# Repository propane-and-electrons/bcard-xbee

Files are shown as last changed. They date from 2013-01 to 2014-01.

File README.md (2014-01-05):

bcard-xbee
----------

Mid-2011, I had the idea of making a PCB business card. At the time I was working on Super Street Fire, and developing a [wireless solenoid controller](https://github.com/propane-and-electrons/wifire16) for triggering flame effects. I took the same basic idea, removed everything unnecessary (including the microcontroller), and set aside an area for contact info. With the remaining space, I found I could fit three optoisolator/MOSFET circuits comfortably.

The end result is this, a three channel wireless solenoid controller.

Yes, it is fully functional.

Please do not call me in the middle of the night and breathe heavily into the phone.

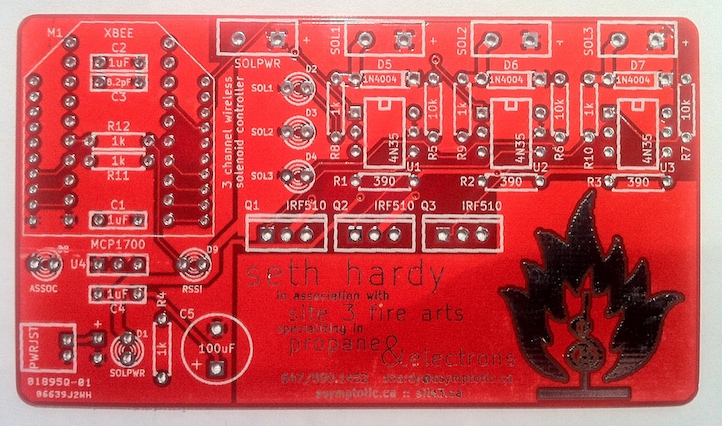
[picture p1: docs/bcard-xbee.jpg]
bcard-xbee photo


### Feature Summary

* No microcontroller!
* Uses XBee (Series 1 or 2, but 1 is easier) DIO lines to trigger outputs
* Three DC load channels switched via MOSFETs
* DC load power is optoisolated from control power
* Status LEDs on each output channel, and for XBee Association/RSSI indicators
* It has all my contact information on it so you know how to get in touch with me

### Design
I do give these cards out to people during normal business card exchange rituals. So, I chose to use only through hole parts: people often have little or no experience assembling electronics, so it was designed to be as easy as possible. XBee radios were also chosen for their ease of use.

The card itself is the same size as a normal business card. I have them made on 0.8mm FR4.

#### Power
The card has two separate power inputs: one for the control system, and one for the solenoid power that it switches. This allows the card to be powered off a 3.7V LiPo battery (with 2 pin JST header) or 3xAA/AAA battery pack, while switching 12V, 24V, or higher voltage DC to activate the solenoids.

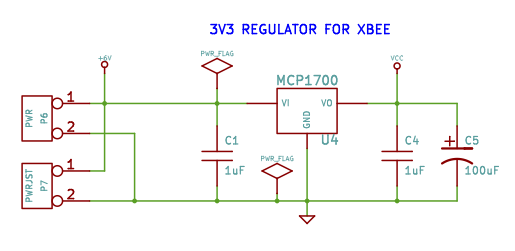
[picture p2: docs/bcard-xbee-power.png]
bcard-xbee photo


Since this was designed for fire art, having a separate solenoid power source allows a deadman switch inline, so the dangerous side can be shut down immediately while keeping the controller side active. The two sides are separated via optoisolators.

#### Data
The card uses an XBee radio (Series 1 or 2) for wireless communication. The card does not have a microcontroller on it: the outputs are triggered directly via DIO lines 0 – 2 of the XBee.

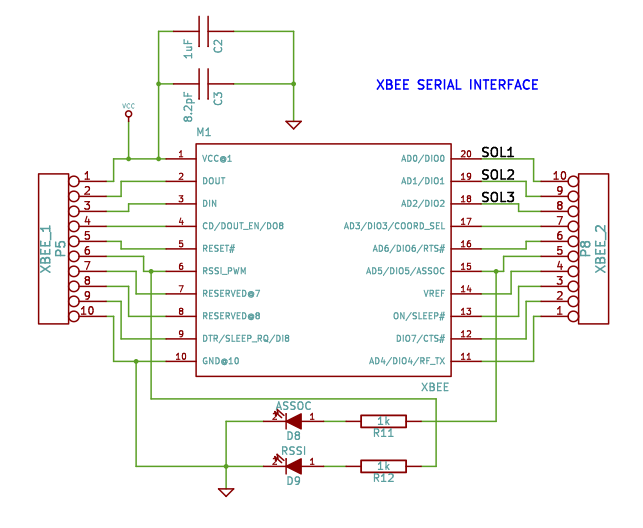
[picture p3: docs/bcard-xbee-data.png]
bcard-xbee photo


This means that a Series 1 radio is preferable, as they can do IO line pairing: change the IO line on the sending radio and it will trigger the output on the receiving radio automatically. Series 2 radios will also work using a remote AT packet to control the line.

#### Solenoid control
The solenoid power is switched using MOSFETs. Each channel has a LED indicator that lights up only when the channel is active.

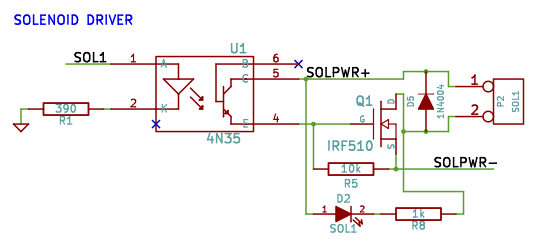
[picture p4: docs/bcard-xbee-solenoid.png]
bcard-xbee photo


### Documents

* [Schematic](docs/bcard-xbee-schematic.pdf)
* [Bill of Materials](docs/bcard-xbee-BOM.csv)

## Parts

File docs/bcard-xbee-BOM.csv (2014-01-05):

Designator | Package | Quantity | Part | Digi-Key Part
C1,C2,C4 | C2 | 3 | 1uF | 445-2858-ND
C3 | C2 | 1 | 8.2pF | 490-3764-ND
C5 | C2V8 | 1 | 100uF | P13459-ND
D1,D2,D3,D4 | LED-3MM | 1 | 3mm LED (red) | 754-1606-ND
D5,D6,D7 | D3 | 3 | 1N4004 | 641-1311-1-ND
D8,D9 | LED-3MM | 1 | 3mm LED (blue) | 754-1596-ND
M1 | XBEE | 1 | XBee Series 1 | XB24-AWI-001-ND
P1,P2,P3,P4 | 5MMSCREWTERM | 1 | 5mm screw terminal | ED2600-ND
P7 | JST2 | 1 | JST2 power header | 455-2257-ND
Q1,Q2,Q3 | TO220GDS_VERT | 3 | IRF510 | IRF510PBF-ND
R1,R2,R3 | R3 | 3 | 390 | 390QBK-ND
R4,R8,R9,R10,R11,R12 | R3 | 6 | 1k | 1.0KQBK-ND
R5,R6,R7 | R3 | 3 | 10k | 10KQBK-ND
U1,U2,U3 | DIP-6__300 | 3 | 4N35 | 516-1557-5-ND
U4 | SIL-3 | 1 | MCP1700 | MCP1700-3302E/TO-ND
XM1 |  | 2 | 2mm 10 pin header | S5751-10-ND
XU1,XU2,XU3 |  | 3 | 6DIP socket | A100203-ND

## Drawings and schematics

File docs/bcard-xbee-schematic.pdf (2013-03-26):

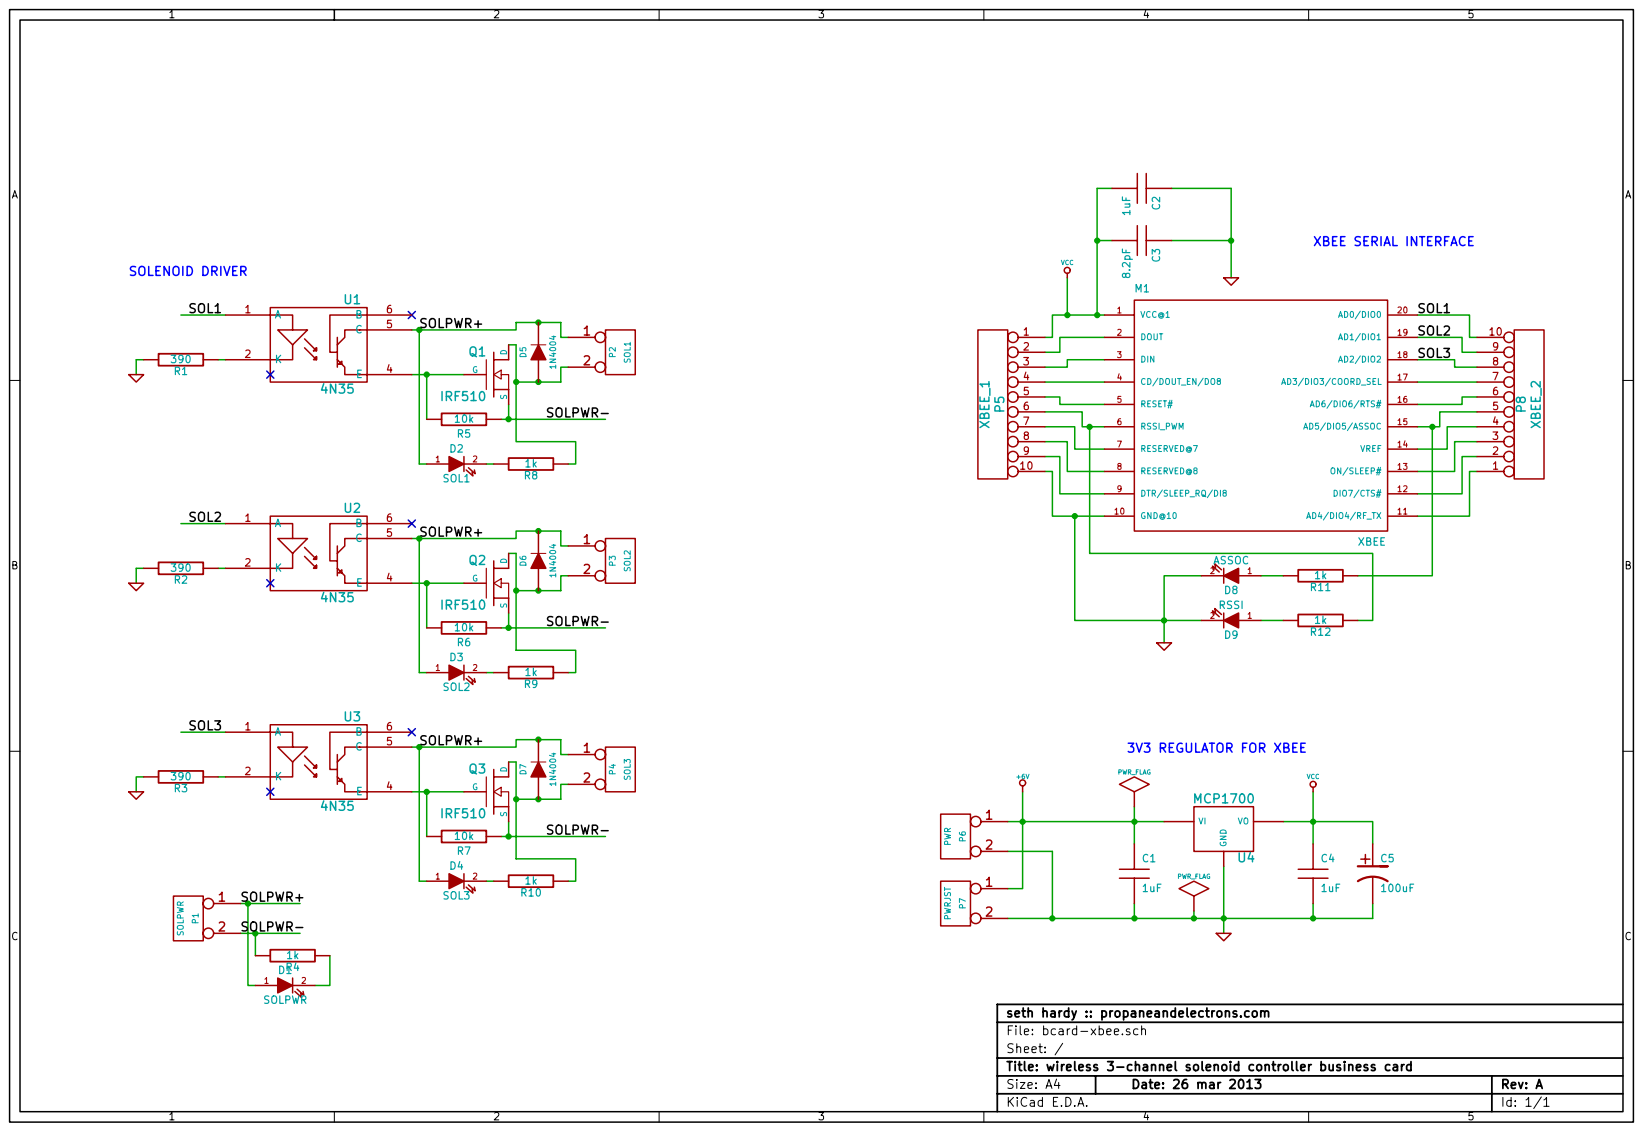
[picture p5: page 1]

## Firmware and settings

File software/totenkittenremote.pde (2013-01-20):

#include <Button.h>
#include <XBee.h>

XBee xbee = XBee();

XBeeAddress64 remoteAddress = XBeeAddress64(0x0013a200, 0x4064F906);
uint8_t on[] = {5};
uint8_t off[] = {4};
uint8_t D0[] = {'D','0'};
RemoteAtCommandRequest reqon  = RemoteAtCommandRequest(remoteAddress, D0, on, 1);
RemoteAtCommandRequest reqoff = RemoteAtCommandRequest(remoteAddress, D0, off, 1);
RemoteAtCommandResponse response;

const int ledPin = 13;
Button button = Button(2, PULLUP);

void setup() {
  pinMode(ledPin, OUTPUT); 
  xbee.begin(57600);
  delay(5000);
}

void loop() {

  if(button.uniquePress()) {
    digitalWrite(ledPin, HIGH);
    xbee.send(reqon);
  }
  else if(button.stateChanged()) {
    digitalWrite(ledPin, LOW);
    xbee.send(reqoff);
  } 
  
}

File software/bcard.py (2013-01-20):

from xbee import ZigBee
import serial
import struct
import re
from time import sleep
from binascii import hexlify

ser = serial.Serial('/dev/tty.xbee', 57600)
xbee = ZigBee(ser, escaped=True)

destname  = ''
destaddr  = ''
destaddrS = ''

# find node
xbee.at(command='ND')
nodefound = 0;
while not nodefound:
	response = xbee.wait_read_frame()
	#print response
	if response['id'] == 'at_response':
		if response['command'] == 'ND':
			parameter = response['parameter']
			destaddrS = parameter[0:2]
			destaddr  = parameter[2:10]
			destname  = parameter[10:]
			index = destname.find('\x00')
			destname = destname[:index]
			print "received node reply for node %s short %s long %s" \
				% (destname, hexlify(destaddrS), hexlify(destaddr))
			nodefound = 1
		
sleep(1)

xbee.send('remote_at', dest_addr_long=destaddr, dest_addr=destaddrS, command='D0', parameter='\x05')
xbee.send('remote_at', dest_addr_long=destaddr, dest_addr=destaddrS, command='D1', parameter='\x05')
xbee.send('remote_at', dest_addr_long=destaddr, dest_addr=destaddrS, command='D2', parameter='\x05')
sleep(5)
xbee.send('remote_at', dest_addr_long=destaddr, dest_addr=destaddrS, command='D0', parameter='\x04')
xbee.send('remote_at', dest_addr_long=destaddr, dest_addr=destaddrS, command='D1', parameter='\x04')
xbee.send('remote_at', dest_addr_long=destaddr, dest_addr=destaddrS, command='D2', parameter='\x04')


while True:

	try:
		xbee.send('remote_at', dest_addr_long=destaddr, dest_addr=destaddrS, command='D0', parameter='\x05')
		sleep(1)
		xbee.send('remote_at', dest_addr_long=destaddr, dest_addr=destaddrS, command='D0', parameter='\x04')
		sleep(1)
		xbee.send('remote_at', dest_addr_long=destaddr, dest_addr=destaddrS, command='D1', parameter='\x05')
		sleep(1)
		xbee.send('remote_at', dest_addr_long=destaddr, dest_addr=destaddrS, command='D1', parameter='\x04')
		sleep(1)
		xbee.send('remote_at', dest_addr_long=destaddr, dest_addr=destaddrS, command='D2', parameter='\x05')
		sleep(1)
		xbee.send('remote_at', dest_addr_long=destaddr, dest_addr=destaddrS, command='D2', parameter='\x04')
		sleep(1)
	except KeyboardInterrupt:
		break


ser.close()

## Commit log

2013-01-20 moving over from google code
    3 channel wireless SSR business card.
    [bcard.brd, bcard.dsn, bcard.sch]
2013-03-13 ignoring common part and footprint libs
2013-03-13 added backannotations, cleared out unneeded files, standardized libraries
    [bcard-xbee.brd, bcard-xbee.sch, bcard.dsn]
2013-03-26 fixing cpol
    [bcard-xbee.sch]
2014-01-05 adding documentation, fixing POWER_HDR part on board
    [bcard-xbee-BOM.csv]
2014-01-05 actually committing the POWER_HDR fix this time
    [bcard-xbee.brd]
